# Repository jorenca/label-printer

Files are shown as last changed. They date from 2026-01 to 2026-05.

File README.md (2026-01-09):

# Tape printer

Reinventing the printer - writing on a roll of tape with a sharpie.

## Overview
This project uses `GRBL` to control a stepper motor and two RC servos in a
CNC-machine-with-rotary-axis style. An `Atmega8` MCU is used to map the step/dir
control pulses from `GRBL` into servo commands.

## Printing
This project provides python code to generate GCODE for printing provided 
text string and font name+size.

Run the code in `print.ipynb` notebook:

```console
cd printing_wizard
jupyter notebook
```

The result of the above is a `text.nc` file that can be used in your
GCODE sender app of choice.

## Build

You will need:
* Arduino Nano
* Atmega8
* A4988 driver
* Nema17 motor (for X axis)
* MG996R servo (for Y axis)
* MG90s servo (for Z axis)
* 12-24V / 4A DC power supply
* 5V buck converter (for servo powering)
* 8mm linear rails (2 pcs, ~15cm each)
* 8mm linear bearings (2 pcs, `SCS8UU` part)
* 8mm skateboard bearings (4 pcs)
* M3 screws up to 30mm, nuts, washers, etc.
* A couple of M4 and M8 bolts, a couple of springs

### Flashing `GRBL`
Check out the latest version of `GRBL`.
Use the config file provided in `grbl/config.h` to replace/merge with the `GRBL` one.
Compile and flash on an Arduino Nano.

#### `GRBL` settings
Apply the `GRBL` settings (steps per mm for each axis, etc.)
listed in `grbl/settings.txt` after flashing the firmware.

### Flashing the `stepper-to-servo` firmware
Open the `stepper-to-servo` Arduino project and compile.
Copy the path to the compiled `stepper-to-servo.ino.hex` from the compiler log.

Attach your programmer to the Atmega8 and from the `avrdude` folder, run:
```console
# Set the fuses for 8MHz internal oscillator
.\avrdude.exe -v -patmega8 -cusbasp -Pusb -U lfuse:w:0xd4:m -U hfuse:w:0xd9:m

# Flash the firmware
.\avrdude.exe -v -patmega8 -cusbasp -Pusb -Uflash:w:PATH_TO_arduino_build/stepper-to-servo.ino.hex:i
```

### Schematic / wiring

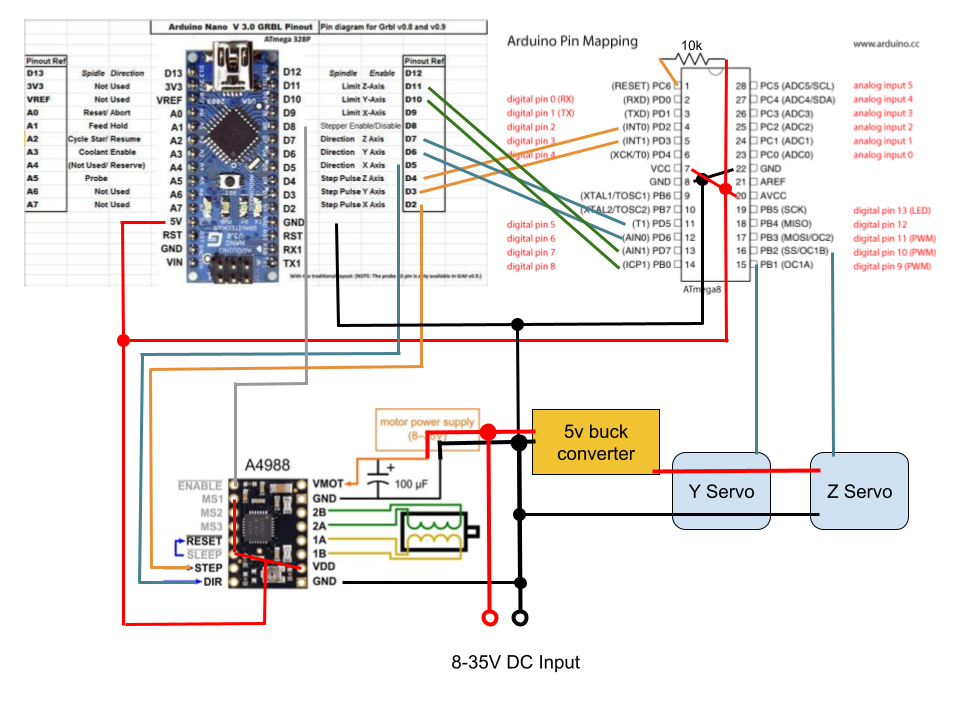
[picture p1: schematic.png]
Schematic


### 3D Models

All `.stl` files are available in the `stls` directory.

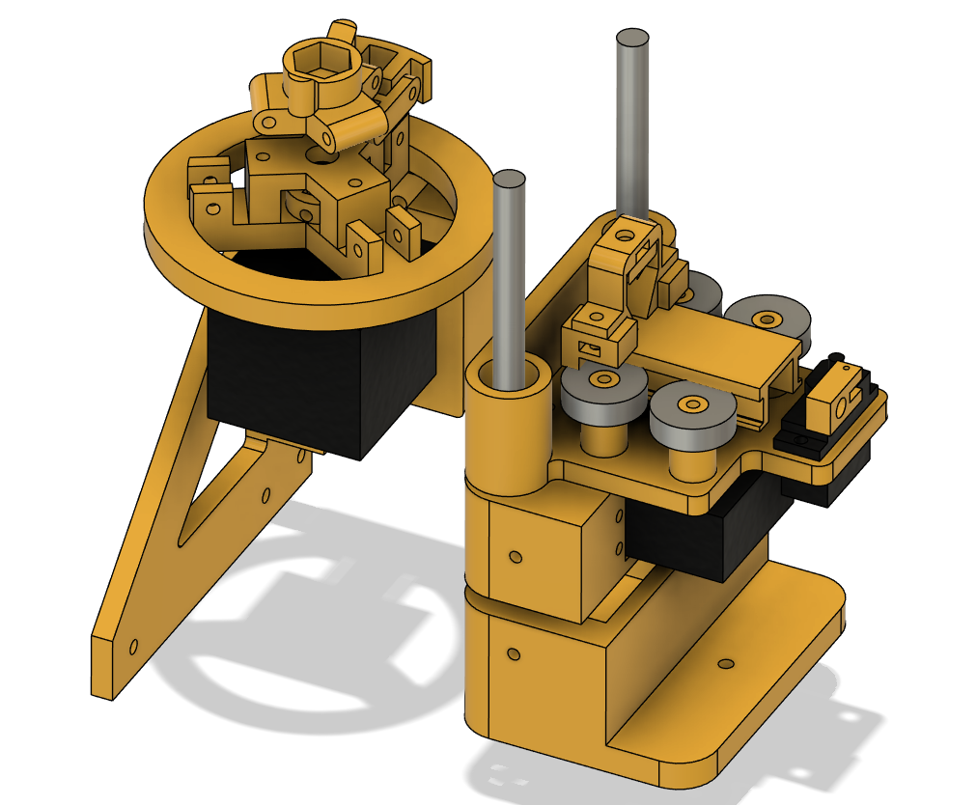
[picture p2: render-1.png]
Rendering 1

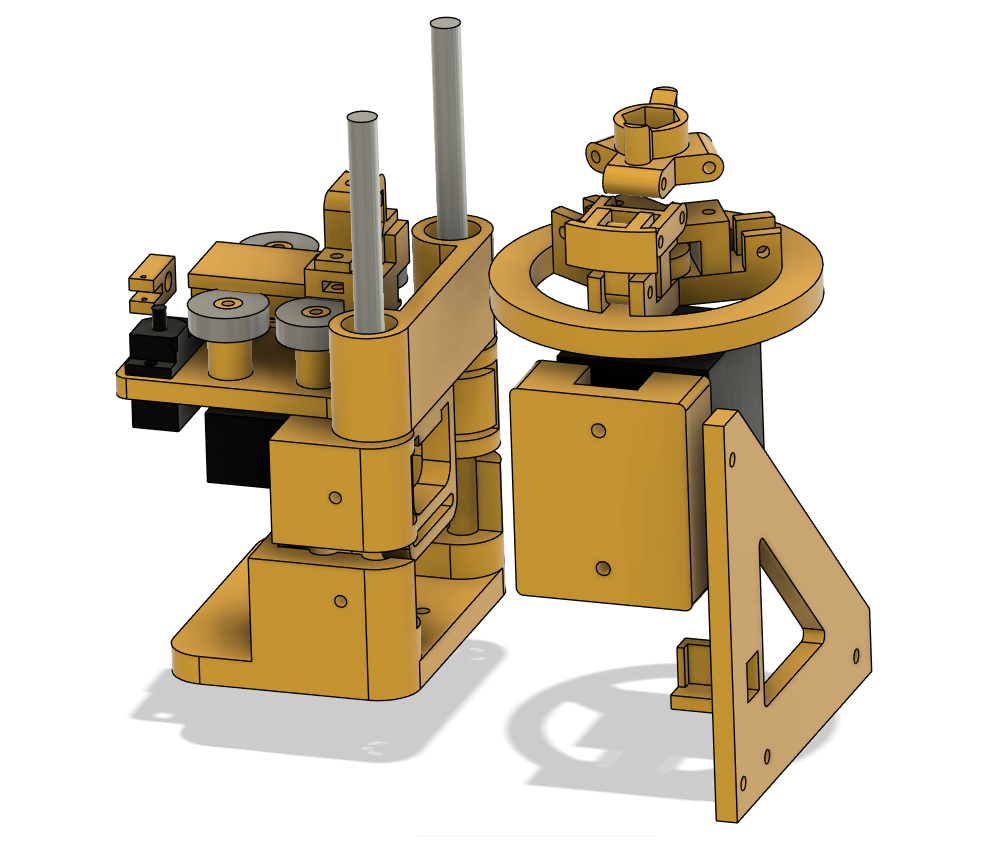
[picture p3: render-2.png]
Rendering 2


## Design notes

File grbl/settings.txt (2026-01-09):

$0 = 10    (Step pulse time, microseconds)
$1 = 25    (Step idle delay, milliseconds)
$2 = 0    (Step pulse invert, mask)
$3 = 2    (Step direction invert, mask)
$4 = 0    (Invert step enable pin, boolean)
$5 = 0    (Invert limit pins, boolean)
$6 = 0    (Invert probe pin, boolean)
$10 = 1    (Status report options, mask)
$11 = 0.010    (Junction deviation, millimeters)
$12 = 0.002    (Arc tolerance, millimeters)
$13 = 0    (Report in inches, boolean)
$20 = 0    (Soft limits enable, boolean)
$21 = 0    (Hard limits enable, boolean)
$22 = 0    (Homing cycle enable, boolean)
$23 = 0    (Homing direction invert, mask)
$24 = 25.000    (Homing locate feed rate, mm/min)
$25 = 500.000    (Homing search seek rate, mm/min)
$26 = 250    (Homing switch debounce delay, milliseconds)
$27 = 1.000    (Homing switch pull-off distance, millimeters)
$30 = 1000    (Maximum spindle speed, RPM)
$31 = 0    (Minimum spindle speed, RPM)
$32 = 0    (Laser-mode enable, boolean)
$100 = 12.000    (X-axis travel resolution, step/mm)
$101 = 10.000    (Y-axis travel resolution, step/mm)
$102 = 10.000    (Z-axis travel resolution, step/mm)
$110 = 2000.000    (X-axis maximum rate, mm/min)
$111 = 2000.000    (Y-axis maximum rate, mm/min)
$112 = 800.000    (Z-axis maximum rate, mm/min)
$120 = 200.000    (X-axis acceleration, mm/sec^2)
$121 = 200.000    (Y-axis acceleration, mm/sec^2)
$122 = 400.000    (Z-axis acceleration, mm/sec^2)
$130 = 200.000    (X-axis maximum travel, millimeters)
$131 = 200.000    (Y-axis maximum travel, millimeters)
$132 = 200.000    (Z-axis maximum travel, millimeters)

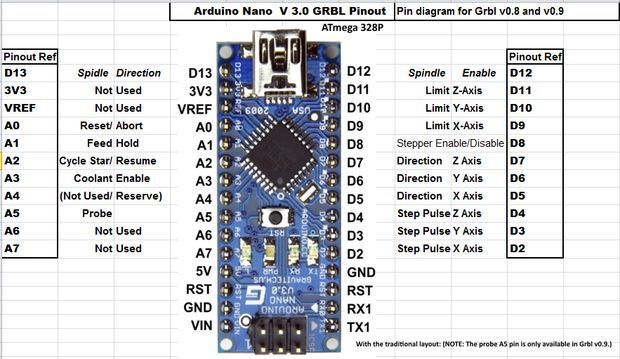
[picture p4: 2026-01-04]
stepper-to-servo/Arduino Nano grbl pinout.jpg

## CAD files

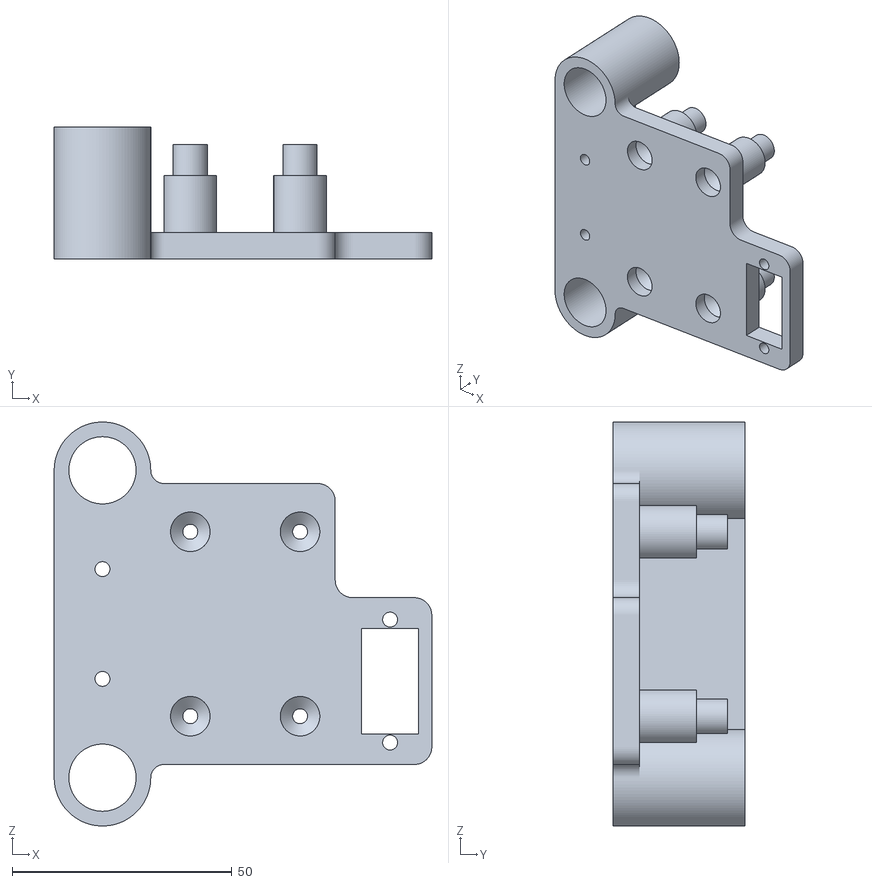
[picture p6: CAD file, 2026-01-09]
stls/Y Axis main.stl
86.0 x 30.0 x 92.0

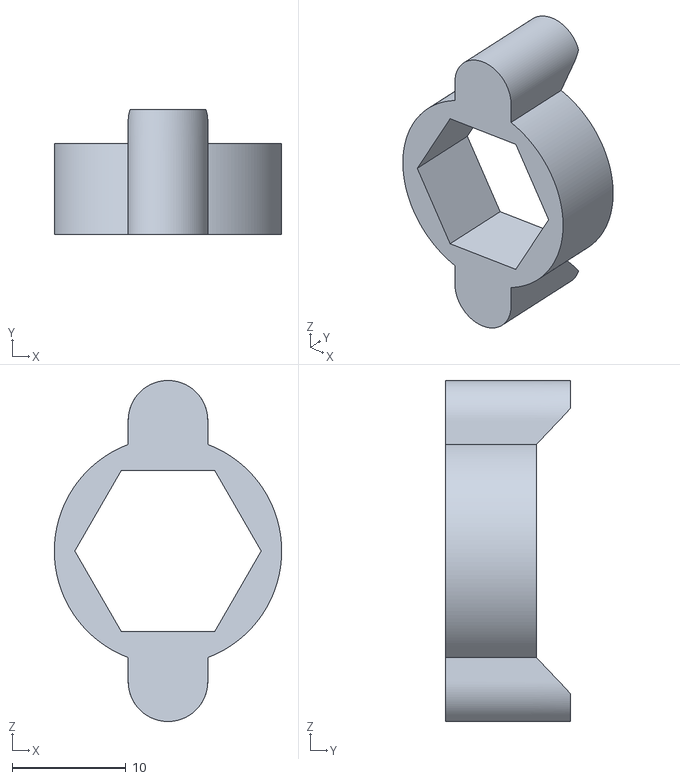
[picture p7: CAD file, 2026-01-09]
stls/Tape tightening butterfly.stl
20.0 x 11.0 x 30.0

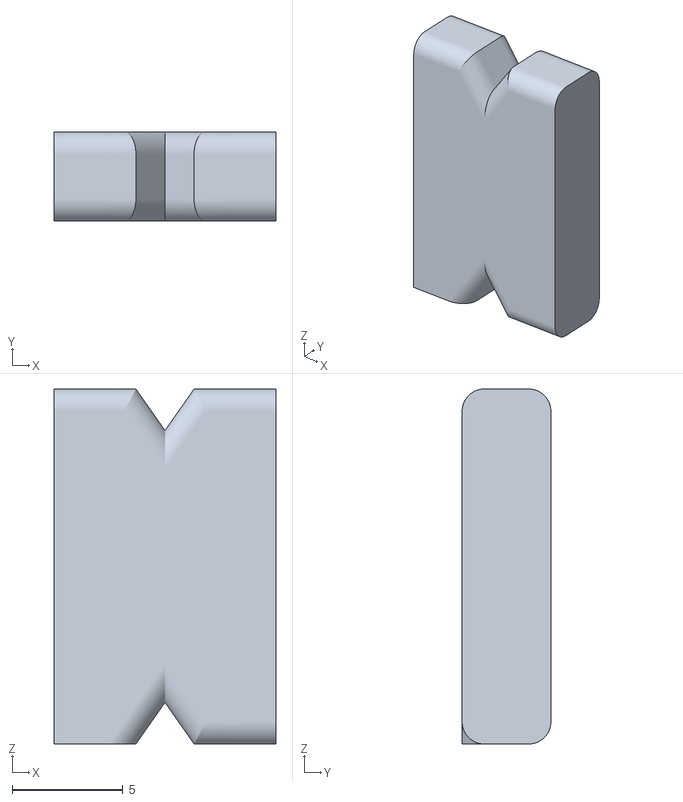
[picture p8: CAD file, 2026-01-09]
stls/pen holder tightener.stl
10.0 x 4.00 x 16.0

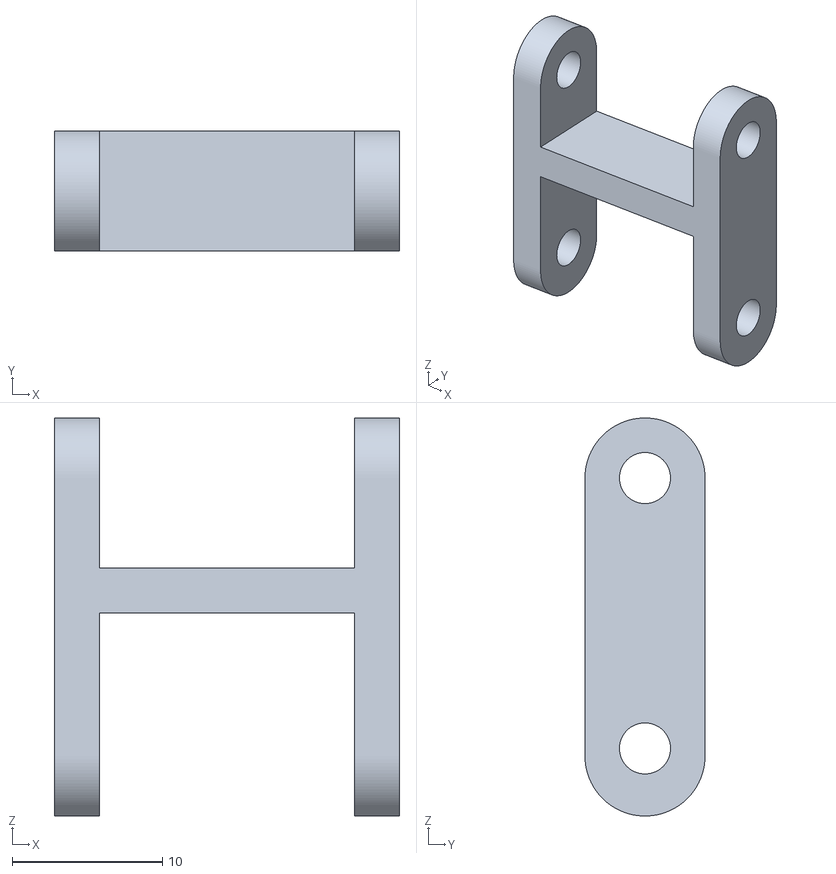
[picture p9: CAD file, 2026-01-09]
stls/Tape holder cross link.stl
23.0 x 8.00 x 26.5

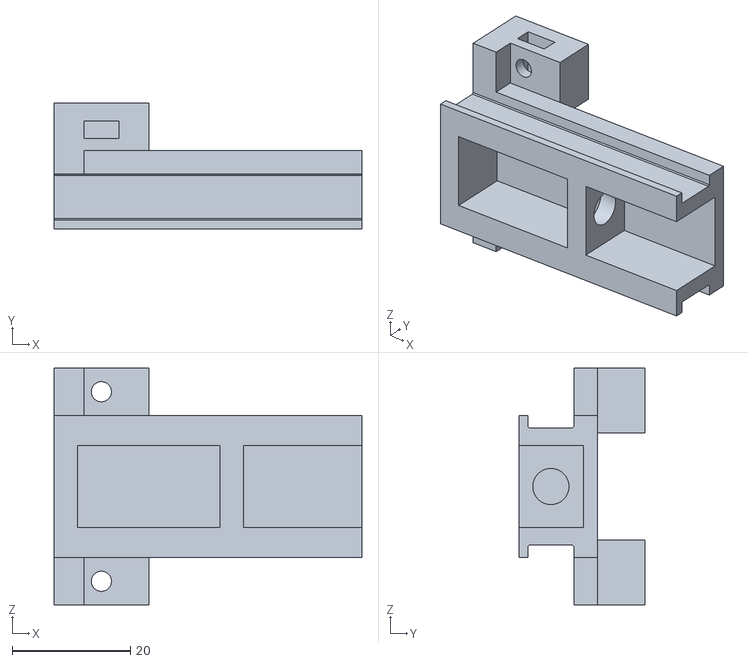
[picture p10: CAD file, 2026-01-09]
stls/Z carriage.stl
52.0 x 21.2 x 40.0

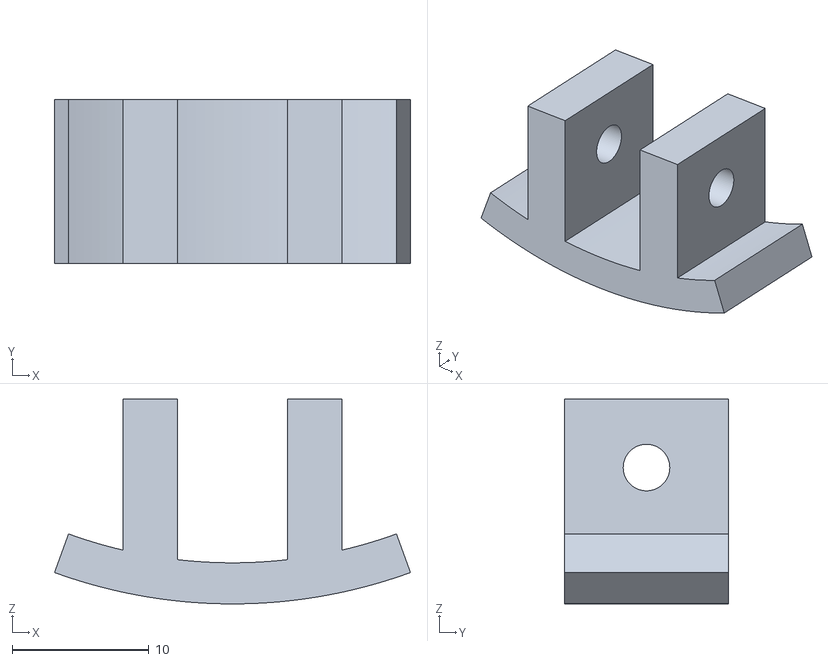
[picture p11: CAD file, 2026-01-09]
stls/Tape holder foot.stl
26.0 x 12.0 x 15.0

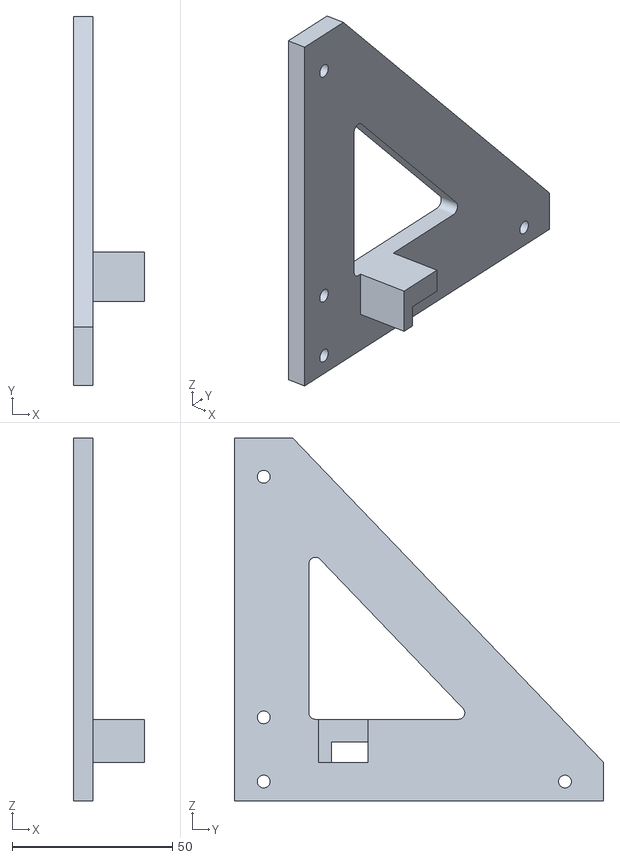
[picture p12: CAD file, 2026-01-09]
stls/Side 90deg support.stl
22.0 x 115.0 x 113.0

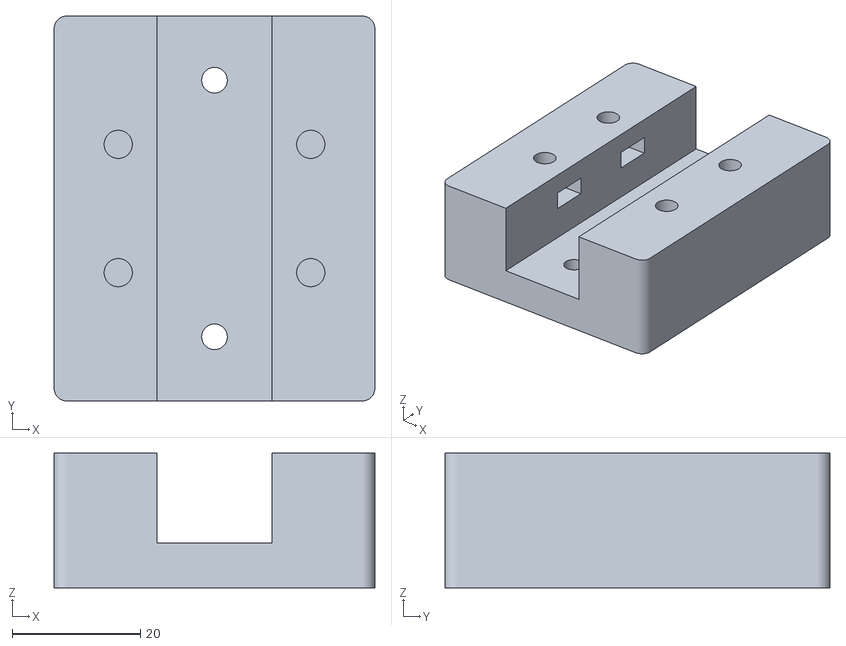
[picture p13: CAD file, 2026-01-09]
stls/X Motor mount.stl
50.0 x 60.0 x 21.0

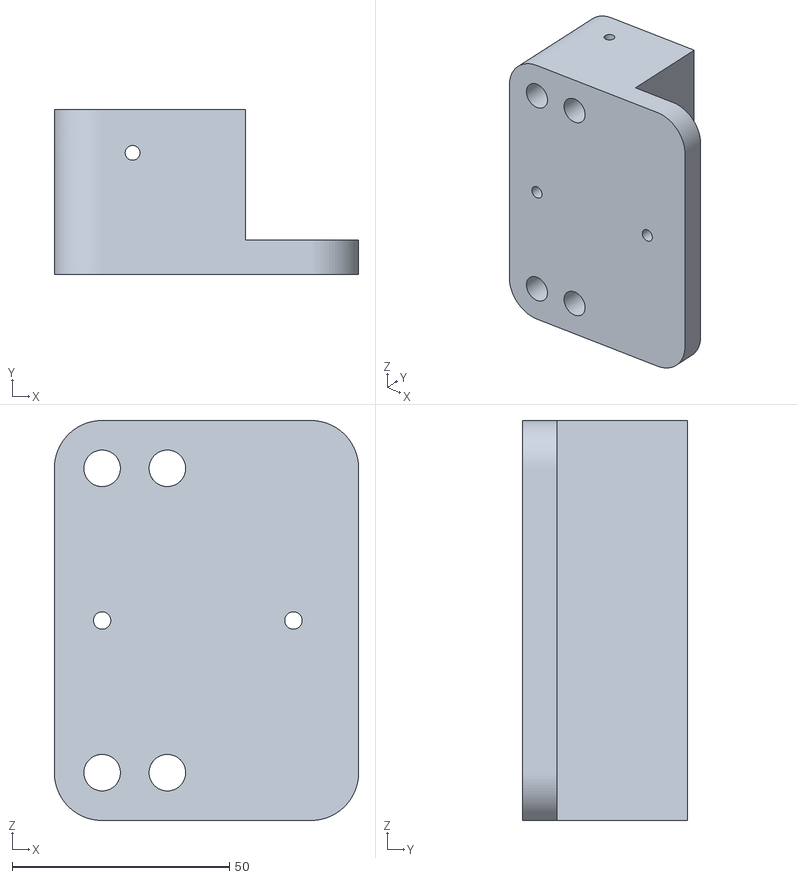
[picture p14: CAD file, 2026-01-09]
stls/Y Axis base mount.stl
70.0 x 38.0 x 92.0

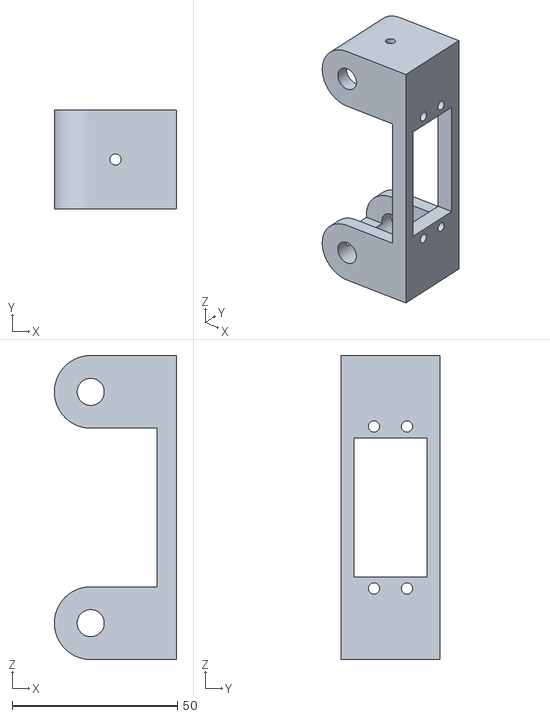
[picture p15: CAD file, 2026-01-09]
stls/Y Axis Servo Mount.stl
37.0 x 30.0 x 92.0

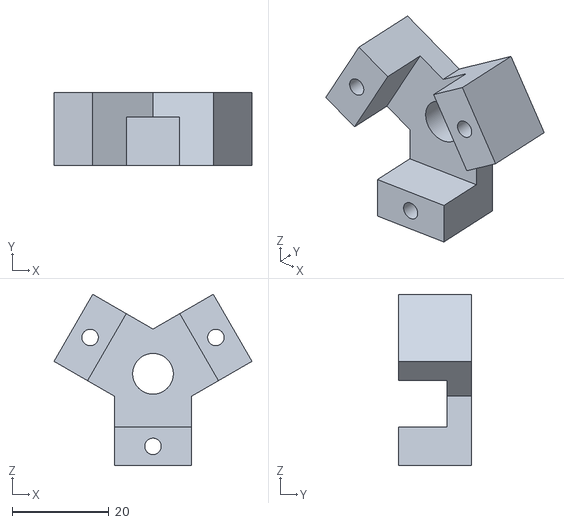
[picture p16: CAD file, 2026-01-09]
stls/Tape holder tightening anchor.stl
40.9 x 15.0 x 35.4

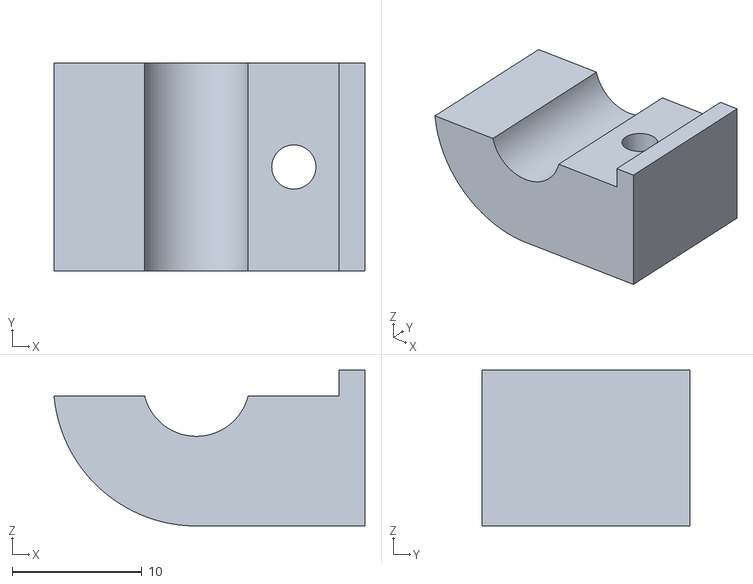
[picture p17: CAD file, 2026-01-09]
stls/Y axis clip.stl
23.9 x 16.0 x 12.0

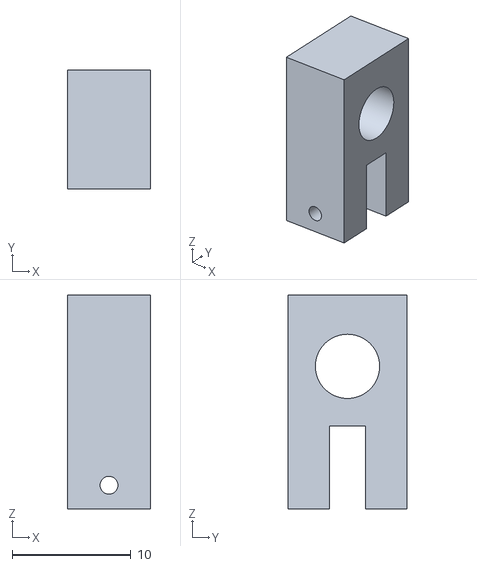
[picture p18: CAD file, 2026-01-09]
stls/z axis servo connector.stl
7.00 x 10.0 x 18.0

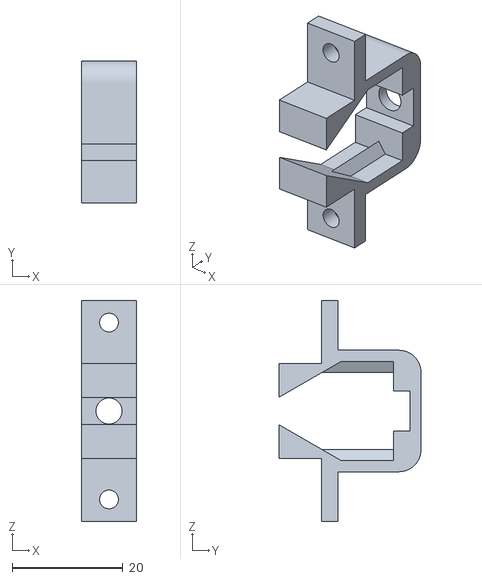
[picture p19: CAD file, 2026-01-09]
stls/pen holder 10-16.stl
10.0 x 25.7 x 40.0

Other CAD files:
stls/scotch yoke.stl
stls/Tape holder foot link.stl
stls/Tape holder tightening plate.stl
stls/Tape holder base.stl

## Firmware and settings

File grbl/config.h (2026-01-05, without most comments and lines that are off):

#define config_h
#include "grbl.h" // For Arduino IDE compatibility.
#define DEFAULTS_GENERIC
#define CPU_MAP_ATMEGA328P // Arduino Uno CPU
#define BAUD_RATE 115200
#define CMD_RESET 0x18 // ctrl-x.
#define CMD_STATUS_REPORT '?'
#define CMD_CYCLE_START '~'
#define CMD_FEED_HOLD '!'
#define CMD_SAFETY_DOOR 0x84
#define CMD_JOG_CANCEL  0x85
#define CMD_DEBUG_REPORT 0x86 // Only when DEBUG enabled, sends debug report in '{}' braces.
#define CMD_FEED_OVR_RESET 0x90         // Restores feed override value to 100%.
#define CMD_FEED_OVR_COARSE_PLUS 0x91
#define CMD_FEED_OVR_COARSE_MINUS 0x92
#define CMD_FEED_OVR_FINE_PLUS  0x93
#define CMD_FEED_OVR_FINE_MINUS  0x94
#define CMD_RAPID_OVR_RESET 0x95        // Restores rapid override value to 100%.
#define CMD_RAPID_OVR_MEDIUM 0x96
#define CMD_RAPID_OVR_LOW 0x97
#define CMD_SPINDLE_OVR_RESET 0x99      // Restores spindle override value to 100%.
#define CMD_SPINDLE_OVR_COARSE_PLUS 0x9A
#define CMD_SPINDLE_OVR_COARSE_MINUS 0x9B
#define CMD_SPINDLE_OVR_FINE_PLUS 0x9C
#define CMD_SPINDLE_OVR_FINE_MINUS 0x9D
#define CMD_SPINDLE_OVR_STOP 0x9E
#define CMD_COOLANT_FLOOD_OVR_TOGGLE 0xA0
#define CMD_COOLANT_MIST_OVR_TOGGLE 0xA1
#define HOMING_INIT_LOCK // Comment to disable
#define HOMING_CYCLE_0 (1<<Z_AXIS)                // REQUIRED: First move Z to clear workspace.
#define HOMING_CYCLE_1 ((1<<X_AXIS)|(1<<Y_AXIS))  // OPTIONAL: Then move X,Y at the same time.
#define N_HOMING_LOCATE_CYCLE 1 // Integer (1-128)
#define N_STARTUP_LINE 2 // Integer (1-2)
#define N_DECIMAL_COORDVALUE_INCH 4 // Coordinate or position value in inches
#define N_DECIMAL_COORDVALUE_MM   3 // Coordinate or position value in mm
#define N_DECIMAL_RATEVALUE_INCH  1 // Rate or velocity value in in/min
#define N_DECIMAL_RATEVALUE_MM    0 // Rate or velocity value in mm/min
#define N_DECIMAL_SETTINGVALUE    3 // Decimals for floating point setting values
#define N_DECIMAL_RPMVALUE        0 // RPM value in rotations per min.
#define MESSAGE_PROBE_COORDINATES // Enabled by default. Comment to disable.
#define SAFETY_DOOR_SPINDLE_DELAY 4.0 // Float (seconds)
#define SAFETY_DOOR_COOLANT_DELAY 1.0 // Float (seconds)
#define CHECK_LIMITS_AT_INIT
#define DEFAULT_FEED_OVERRIDE           100 // 100%. Don't change this value.
#define MAX_FEED_RATE_OVERRIDE          200 // Percent of programmed feed rate (100-255). Usually 120% or 200%
#define MIN_FEED_RATE_OVERRIDE           10 // Percent of programmed feed rate (1-100). Usually 50% or 1%
#define FEED_OVERRIDE_COARSE_INCREMENT   10 // (1-99). Usually 10%.
#define FEED_OVERRIDE_FINE_INCREMENT      1 // (1-99). Usually 1%.
#define DEFAULT_RAPID_OVERRIDE  100 // 100%. Don't change this value.
#define RAPID_OVERRIDE_MEDIUM    50 // Percent of rapid (1-99). Usually 50%.
#define RAPID_OVERRIDE_LOW       25 // Percent of rapid (1-99). Usually 25%.
#define DEFAULT_SPINDLE_SPEED_OVERRIDE    100 // 100%. Don't change this value.
#define MAX_SPINDLE_SPEED_OVERRIDE        200 // Percent of programmed spindle speed (100-255). Usually 200%.
#define MIN_SPINDLE_SPEED_OVERRIDE         10 // Percent of programmed spindle speed (1-100). Usually 10%.
#define SPINDLE_OVERRIDE_COARSE_INCREMENT  10 // (1-99). Usually 10%.
#define SPINDLE_OVERRIDE_FINE_INCREMENT     1 // (1-99). Usually 1%.
#define RESTORE_OVERRIDES_AFTER_PROGRAM_END // Default enabled. Comment to disable.
#define REPORT_FIELD_BUFFER_STATE // Default enabled. Comment to disable.
#define REPORT_FIELD_PIN_STATE // Default enabled. Comment to disable.
#define REPORT_FIELD_CURRENT_FEED_SPEED // Default enabled. Comment to disable.
#define REPORT_FIELD_WORK_COORD_OFFSET // Default enabled. Comment to disable.
#define REPORT_FIELD_OVERRIDES // Default enabled. Comment to disable.
#define REPORT_FIELD_LINE_NUMBERS // Default enabled. Comment to disable.
#define REPORT_OVR_REFRESH_BUSY_COUNT 20  // (1-255)
#define REPORT_OVR_REFRESH_IDLE_COUNT 10  // (1-255) Must be less than or equal to the busy count
#define REPORT_WCO_REFRESH_BUSY_COUNT 30  // (2-255)
#define REPORT_WCO_REFRESH_IDLE_COUNT 10  // (2-255) Must be less than or equal to the busy count
#define ACCELERATION_TICKS_PER_SECOND 100
#define ADAPTIVE_MULTI_AXIS_STEP_SMOOTHING  // Default enabled. Comment to disable.
#define TOOL_LENGTH_OFFSET_AXIS Z_AXIS // Default z-axis. Valid values are X_AXIS, Y_AXIS, or Z_AXIS.
#define MINIMUM_JUNCTION_SPEED 0.0 // (mm/min)
#define MINIMUM_FEED_RATE 1.0 // (mm/min)
#define N_ARC_CORRECTION 12 // Integer (1-255)
#define ARC_ANGULAR_TRAVEL_EPSILON 5E-7 // Float (radians)
#define DWELL_TIME_STEP 50 // Integer (1-255) (milliseconds)
#define ENABLE_RESTORE_EEPROM_WIPE_ALL         // '$RST=*' Default enabled. Comment to disable.
#define ENABLE_RESTORE_EEPROM_DEFAULT_SETTINGS // '$RST=$' Default enabled. Comment to disable.
#define ENABLE_RESTORE_EEPROM_CLEAR_PARAMETERS // '$RST=#' Default enabled. Comment to disable.
#define ENABLE_BUILD_INFO_WRITE_COMMAND // '$I=' Default enabled. Comment to disable.
#define FORCE_BUFFER_SYNC_DURING_EEPROM_WRITE // Default enabled. Comment to disable.
#define FORCE_BUFFER_SYNC_DURING_WCO_CHANGE // Default enabled. Comment to disable.
#define PARKING_AXIS Z_AXIS // Define which axis that performs the parking motion
#define PARKING_TARGET -5.0 // Parking axis target. In mm, as machine coordinate [-max_travel,0].
#define PARKING_RATE 500.0 // Parking fast rate after pull-out in mm/min.
#define PARKING_PULLOUT_RATE 100.0 // Pull-out/plunge slow feed rate in mm/min.
#define PARKING_PULLOUT_INCREMENT 5.0 // Spindle pull-out and plunge distance in mm. Incremental distance.
#define DISABLE_LASER_DURING_HOLD // Default enabled. Comment to disable.
#define N_PIECES 4  // Integer (1-4). Number of piecewise lines used in script solution.
#define RPM_MAX  11686.4  // Max RPM of model. $30 > RPM_MAX will be limited to RPM_MAX.
#define RPM_MIN  202.5    // Min RPM of model. $31 < RPM_MIN will be limited to RPM_MIN.
#define RPM_POINT12  6145.4  // Used N_PIECES >=2. Junction point between lines 1 and 2.
#define RPM_POINT23  9627.8  // Used N_PIECES >=3. Junction point between lines 2 and 3.
#define RPM_POINT34  10813.9 // Used N_PIECES = 4. Junction point between lines 3 and 4.
#define RPM_LINE_A1  3.197101e-03  // Used N_PIECES >=1. A and B constants of line 1.
#define RPM_LINE_B1  -3.526076e-1
#define RPM_LINE_A2  1.722950e-2   // Used N_PIECES >=2. A and B constants of line 2.
#define RPM_LINE_B2  8.588176e+01
#define RPM_LINE_A3  5.901518e-02  // Used N_PIECES >=3. A and B constants of line 3.
#define RPM_LINE_B3  4.881851e+02
#define RPM_LINE_A4  1.203413e-01  // Used N_PIECES = 4. A and B constants of line 4.
#define RPM_LINE_B4  1.151360e+03
#define DUAL_AXIS_SELECT  X_AXIS  // Must be either X_AXIS or Y_AXIS
#define DUAL_AXIS_HOMING_FAIL_AXIS_LENGTH_PERCENT  5.0  // Float (percent)
#define DUAL_AXIS_HOMING_FAIL_DISTANCE_MAX  25.0  // Float (mm)
#define DUAL_AXIS_HOMING_FAIL_DISTANCE_MIN  2.5  // Float (mm)
#define DUAL_AXIS_CONFIG_PROTONEER_V3_51    // Uncomment to select. Comment other configs.

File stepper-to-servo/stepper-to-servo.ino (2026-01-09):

#include <Arduino.h>
#include <Servo.h>





int linearMapPercentage(float percent, int servoMinDeg, int servoMaxDeg) {
    return map(
        percent * 10000,
        0 * 10000,
        1 * 10000,
        servoMinDeg,
        servoMaxDeg
    );
  
}


int scotchYokeMapPercentage(float percent, int servoMinDeg, int servoMaxDeg) {
    
//    float minTheta = servoMinDeg * PI / 180.0 - (PI / 2.0f); 
//    float maxTheta = servoMaxDeg * PI / 180.0 - (PI / 2.0f);
//    float minDist = sin(minTheta);
//    float maxDist = sin(maxTheta);
//    float totalTravel = maxDist - minDist;
//    float travelDist = minDist + percent * totalTravel;

        // Inverse Scotch yoke: linear position -> crank angle
    // θ in range [-π/2, +π/2]
    float theta = asin(2.0f * percent - 1.0f);

    // Normalize angle to [0.0, 1.0]
    float angleNorm = (theta + (PI / 2.0f)) / PI;

    // Map angle to servo degrees
    // Assuming min and max servo degrees correspond to bottom and top positions
    return linearMapPercentage(angleNorm, servoMinDeg, servoMaxDeg);
    //return (theta + (PI / 2.0f)) * 180.0 / PI;
  
}


class ServoStepper {
public:
    // Public endstop indicators
    bool endstopPlus  = false;
    bool endstopMinus = false;

    // Constructor
    ServoStepper(
        uint8_t servoPin,
        int (*mappingStrategyFn)(float, int, int),
        int servoMinDeg = 0,
        int servoMaxDeg = 180,
        int totalSteps = 100
    )
        : _pin(servoPin),
          _mappingStrategy(mappingStrategyFn),
          _servoMin(servoMinDeg),
          _servoMax(servoMaxDeg),
          _totalSteps(totalSteps)
    {
    }

    void begin() {
        _servo.attach(_pin);
        step(0);
    }

    void step(int32_t stepsCount) {

        float percent = (float)stepsCount / (float)_totalSteps;
        
        endstopPlus = stepsCount >= _totalSteps;
        endstopMinus = stepsCount <= 0;

        int currentAngleDeg = (*_mappingStrategy)(
            percent,
            _servoMin,
            _servoMax
        );
        
        _servo.write(currentAngleDeg);
    }

private:
    Servo _servo;
    uint8_t _pin;

    int _servoMin;
    int _servoMax;
    int _totalSteps;
    int (*_mappingStrategy)(float, int, int);

};

//////////////////////////////////////////////

#define CHAN_0_STEP_PIN 3  // needs interrupt pin
#define CHAN_0_DDR DDRD
#define CHAN_0_DIR_PORT PIND
#define CHAN_0_DIR_PIN PD6
#define CHAN_0_ENDSTOP_PIN 8

#define CHAN_0_SERVO_OUT_PIN 9

#define CHAN_1_STEP_PIN 2  // needs interrupt pin
#define CHAN_1_DDR DDRD
#define CHAN_1_DIR_PORT PIND
#define CHAN_1_DIR_PIN PD5
#define CHAN_1_ENDSTOP_PIN 7

#define CHAN_1_SERVO_OUT_PIN 10

#define CHAN_0_TOTAL_STEPS 460
#define CHAN_1_TOTAL_STEPS 100

volatile int32_t stepCountA = 0;
volatile int32_t stepCountB = 0;

void ISR_stepA() {
    // digitalRead is too slow?
    //bool dir = digitalRead(CHAN_0_DIR_PIN);
    bool dir = CHAN_0_DIR_PORT & _BV(CHAN_0_DIR_PIN);
    
    //constrain() is not ISR-safe (it’s a macro with comparisons).
    //stepCountA = constrain(stepCountA, 0, CHAN_0_TOTAL_STEPS);
    if (dir) {
        if (stepCountA < CHAN_0_TOTAL_STEPS) stepCountA++;
    } else {
        if (stepCountA > 0) stepCountA--;
    }
}

void ISR_stepB() {
    // digitalRead is too slow?
    //bool dir = digitalRead(CHAN_1_DIR_PIN);
    bool dir = CHAN_1_DIR_PORT & _BV(CHAN_1_DIR_PIN);

    
    //constrain() is not ISR-safe (it’s a macro with comparisons).
    //stepCountB = constrain(stepCountB, 0, CHAN_1_TOTAL_STEPS);
    if (dir) {
        if (stepCountB < CHAN_1_TOTAL_STEPS) stepCountB++;
    } else {
        if (stepCountB > 0) stepCountB--;
    }
}


ServoStepper chanAServo(
    CHAN_0_SERVO_OUT_PIN,
    scotchYokeMapPercentage, //linearMapPercentage,
    0, 180,
    CHAN_0_TOTAL_STEPS
);

ServoStepper chanBServo(
    CHAN_1_SERVO_OUT_PIN,
    linearMapPercentage,
    150, 60,
    CHAN_1_TOTAL_STEPS
);


void setup() {
    
    pinMode(CHAN_0_STEP_PIN, INPUT);
    pinMode(CHAN_1_STEP_PIN, INPUT);

    attachInterrupt(digitalPinToInterrupt(CHAN_0_STEP_PIN), ISR_stepA, RISING);
    attachInterrupt(digitalPinToInterrupt(CHAN_1_STEP_PIN), ISR_stepB, RISING);
    
    CHAN_0_DDR &= ~_BV(CHAN_0_DIR_PIN);   // clear bit → INPUT
    CHAN_1_DDR &= ~_BV(CHAN_1_DIR_PIN);   // clear bit → INPUT
    
    pinMode(CHAN_0_ENDSTOP_PIN, OUTPUT);
    pinMode(CHAN_1_ENDSTOP_PIN, OUTPUT);
    
    chanAServo.begin();
    chanBServo.begin();
}


void loop() {

    noInterrupts();
    int32_t stepsA = stepCountA;
    int32_t stepsB = stepCountB;
    interrupts();
    
    chanAServo.step(stepsA);
    chanBServo.step(stepsB);
    
    digitalWrite(CHAN_0_ENDSTOP_PIN, chanAServo.endstopMinus || chanAServo.endstopPlus);
    digitalWrite(CHAN_1_ENDSTOP_PIN, chanBServo.endstopMinus || chanBServo.endstopPlus);
    delay(20);

}

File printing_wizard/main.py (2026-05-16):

#!/usr/bin/env python3

import serial
import serial.tools.list_ports
import time
import sys
import os

from gcode_conversion import make_text_gcode, DEFAULT_FONT, DEFAULT_FONT_SIZE


# ============================
# SERIAL CONFIGURATION
# ============================
BAUDRATE = 115200
SERIAL_TIMEOUT = 0.1  # 100ms timeout for readline

JOG_FEED = 1000      # mm/min
JOG_STEP = 1.0       # mm


if os.name == "nt":
    import msvcrt

    def get_key():
        if msvcrt.kbhit():
            return msvcrt.getch().decode(errors="ignore")
        return None
else:
    import termios
    import tty
    import select

    class UnixKeyReader:
        def __enter__(self):
            self.fd = sys.stdin.fileno()
            self.old = termios.tcgetattr(self.fd)
            tty.setcbreak(self.fd)
            return self

        def __exit__(self, *_):
            termios.tcsetattr(self.fd, termios.TCSADRAIN, self.old)

        def get_key(self):
            r, _, _ = select.select([sys.stdin], [], [], 0)
            if r:
                return sys.stdin.read(1)
            return None


# ============================
# SERIAL UTILITIES
# ============================
def list_serial_ports():
    ports = list(serial.tools.list_ports.comports())
    if not ports:
        print("No serial ports found.")
        sys.exit(1)
    return ports


def select_serial_port(ports):
    print("\nAvailable serial ports:")
    for i, p in enumerate(ports):
        print(f"  [Option {i+1}] {p.device} - {p.description}")

    while True:
        try:
            idx = int(input("Select option: "))
            return ports[idx-1].device
        except (ValueError, IndexError):
            print("Invalid selection.")


def open_grbl(port):
    ser = serial.Serial(port, BAUDRATE, timeout=SERIAL_TIMEOUT)
    time.sleep(2)
    ser.write(b"\r\n\r\n")
    time.sleep(1)
    ser.reset_input_buffer()
    print("Connected to GRBL.")
    return ser


# ============================
# GRBL COMMUNICATION
# ============================
def send_line(ser, line):
    ser.write((line + "\n").encode())


def jog(ser, x: float = 0, y: float = 0, z: float = 0):
    cmd = f"$J=G91 X{x:.3f} Y{y:.3f} Z{z:.3f} F{JOG_FEED}"
    send_line(ser, cmd)


def reset_zero(ser, jog_to_start: bool = False) -> None:
    if jog_to_start:
        send_line(ser, "G0 Y0 Z0")
    send_line(ser, "G92 X0 Y0 Z0")


# ============================
# REAL-TIME JOGGING
# ============================
def jogging_loop(ser):
    print("""
Jog the pen to the lower left corner of the label, with the pen a couple of millimeters above it.

Jogging Controls:
  W/S: Raise/lower pen
  A/D: Rotate tape
  R/F: Move pen away or towards tape
  
When ready, press:
  Z: Set work zero and proceed with printing
  Q: Quit program
""")

    step = JOG_STEP

    if os.name == "nt":
        key_reader = None
    else:
        key_reader = UnixKeyReader()
        key_reader.__enter__()

    try:
        while True:
            key = get_key() if os.name == "nt" else key_reader.get_key()

            if not key:
                time.sleep(0.01)
                continue

            key = key.lower()

            if key == "w":
                jog(ser, y=step)
            elif key == "s":
                jog(ser, y=-step)
            elif key == "a":
                jog(ser, x=-step)
            elif key == "d":
                jog(ser, x=step)
            elif key == "r":
                jog(ser, z=step/2)
            elif key == "f":
                jog(ser, z=-step/2)
            elif key == "z":
                reset_zero(ser)
                print("Work zero set.")
                return
            elif key == "q":
                print("Exiting program.")
                sys.exit(0)

    finally:
        if key_reader:
            key_reader.__exit__(None, None, None)


# ============================
# STUPID SIMPLE PING-PONG STREAMER
# ============================
def stream_gcode(ser, gcode_lines):

    # Clear out any leftover 'ok' responses from jogging or zeroing commands
    ser.reset_input_buffer()

    # Normalize input to a list of individual lines
    if isinstance(gcode_lines, str):
        raw_lines = gcode_lines.splitlines()
    else:
        raw_lines = []
        for item in gcode_lines:
            raw_lines.extend(str(item).splitlines())

    for raw_line in raw_lines:
        line = raw_line.strip()

        # Skip empty lines and comments
        if not line or line.startswith(";") or line.startswith("("):
            continue
        if ";" in line:
            line = line.split(";")[0].strip()

        # Send the line to GRBL
        #print(f">> {line}")
        send_line(ser, line)

        # Synchronous block: Wait right here until GRBL answers this exact line
        while True:
            resp = ser.readline().decode(errors="ignore").strip()

            if not resp:
                continue  # Serial timeout hit with no data, keep waiting

            if "ok" in resp:
                break  # GRBL approved it! Break this inner loop and send next line
            elif "error" in resp:
                print(f"[!] GRBL Error: {resp} on line: {line}")
                break  # Log the error and move on to keep it running

    print("G-code completed successfully.")


def print_loop(serial_connection):
    font = input(f'Select font (leave empty for {DEFAULT_FONT}): ')
    font_size = input(f'Select font size in mm (leave empty for {DEFAULT_FONT_SIZE}mm): ')
    should_preview = input('Show preview (y/N)? ').lower() == 'y'
    print()

    while True:
        text = input("Text to print: ").strip()
        gcode = make_text_gcode(text, font, font_size, should_preview)

        # Ensure GRBL clears its buffer before we zero and start
        time.sleep(0.1)
        reset_zero(serial_connection)
        time.sleep(0.1)

        stream_gcode(serial_connection, gcode)

        should_continue = input('\nPrint another (Y), use different settings (D) or quit (anything else)? ').lower()

        if should_continue == 'y':
            print()
            continue
        elif should_continue == 'd':
            print()
            print_loop(serial_connection)
        else:
            print("Exiting")
            sys.exit(0)


def main():
    ports = list_serial_ports()
    port = select_serial_port(ports)
    print("Selected port " + port)
    ser = open_grbl(port)

    jogging_loop(ser)
    print_loop(ser)

    ser.close()
    print("Connection closed.")


if __name__ == "__main__":
    main()
>>>>>>> Implement a simple printing command line utility

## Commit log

2026-01-03 Initial import of stepper-to-servo code
    [atmega8 set fuse to 8mhz internal magic params.txt]
2026-01-03 Improve servo code to use floats
2026-01-04 Add stepper-to-servo code for mapping servo position according to scotch yoke mechanics.
2026-01-05 Latest fixes to stepper-to-servo code, also including grbl config file
    [config.h]
2026-01-09 Fix step drifting in stepper-to-servo using interrupts
    [stepper-to-servo.ino]
2026-01-09 Add printing wizard (gcode generation based on font+size) notebook
2026-01-09 Add documentation
    [atmega8 set fuse to 8mhz internal magic params.txt]
2026-01-09 Add documentation and stls
    [Side 90deg support.stl, Tape holder base.stl, Tape holder cross link.stl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]
2026-01-09 Add GRBL settings
2026-05-09 Add UV package management for the printing wizard script
2026-05-16 Implement a simple printing command line utility

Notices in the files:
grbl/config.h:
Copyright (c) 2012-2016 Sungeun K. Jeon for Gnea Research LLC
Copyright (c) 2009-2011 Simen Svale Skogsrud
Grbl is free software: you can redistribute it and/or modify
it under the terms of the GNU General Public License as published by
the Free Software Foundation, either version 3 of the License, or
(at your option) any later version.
